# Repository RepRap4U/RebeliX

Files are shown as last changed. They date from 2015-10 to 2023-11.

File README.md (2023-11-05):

RebeliX X2
=======
RebeliX X2 – nová verze 3D tiskárny RebeliX. Tiskárna je šířena pod licencí GPLv3. 3D model, návod a seznam materiálu na stavbu naleznete ve složce "Manuals". Tiskárna je původně inspirovaná konstrukcemi Rebel II a Průša i3.

RebeliX X2 3D model tiskarny

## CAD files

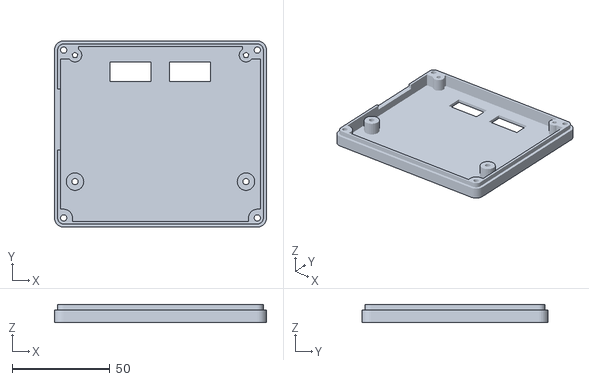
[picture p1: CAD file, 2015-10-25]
src/Doplnky/LCD/Case_for_the_Full_Graphic_Smart_LCD_Controller/Case_for_the_Full_Graphic_Smart_LCD_Controller-Bottom_Case_FGD.stl
108.6 x 95.4 x 9.30

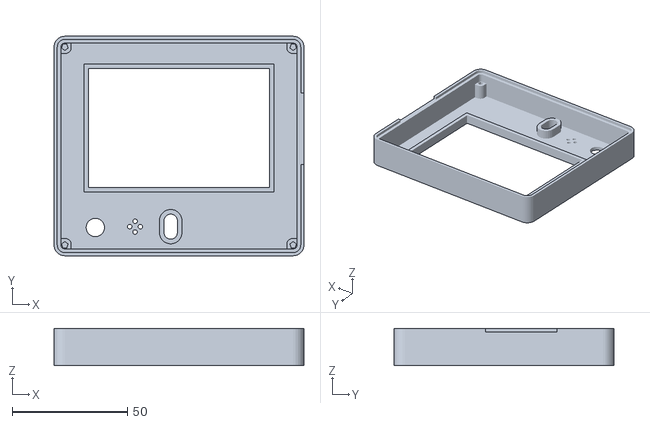
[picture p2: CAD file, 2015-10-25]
src/Doplnky/LCD/Case_for_the_Full_Graphic_Smart_LCD_Controller/Case_for_the_Full_Graphic_Smart_LCD-Top_Case_FGD.stl
108.6 x 95.4 x 16.1

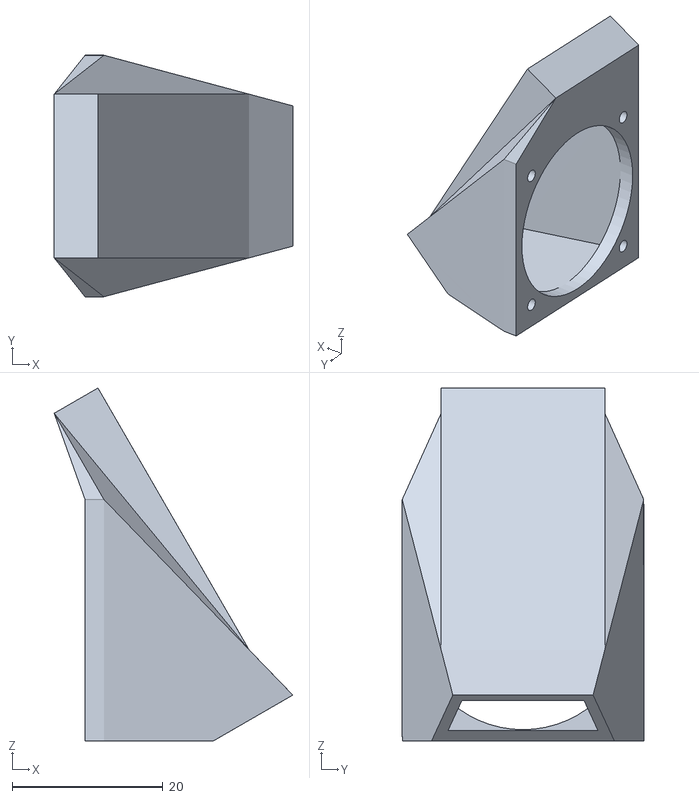
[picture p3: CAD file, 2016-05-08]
src/Extruder_filament_1.75mm/_Dual_experimental/inc/Fan_duct_30x30mm_base.stl
31.6 x 32.0 x 46.8

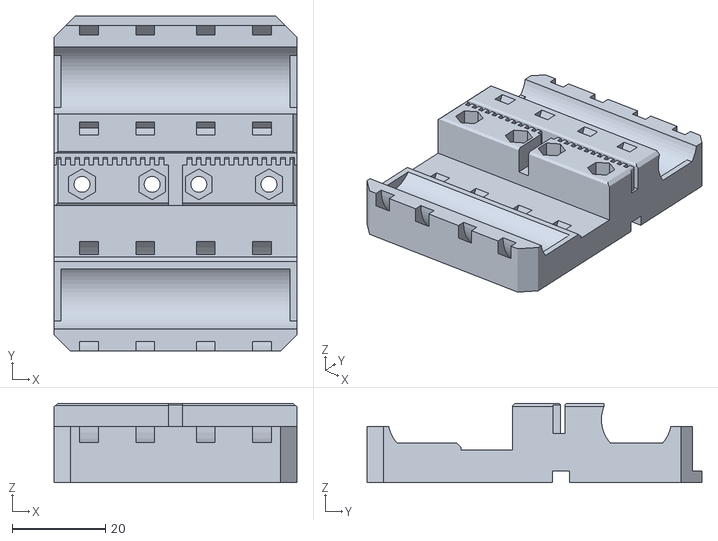
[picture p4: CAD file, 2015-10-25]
src/STLs/x-carriage-dual_GT2.stl
52.0 x 71.7 x 17.0

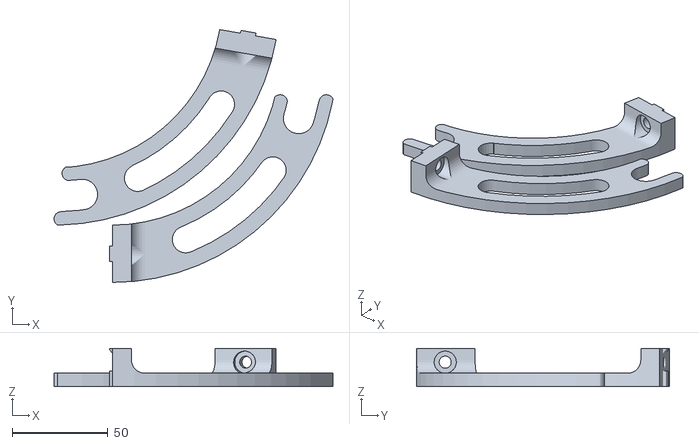
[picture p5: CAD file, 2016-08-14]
STL soubory/Doplnky/Drzak civky dual/spool-holder-dual.stl
146.0 x 132.3 x 20.0

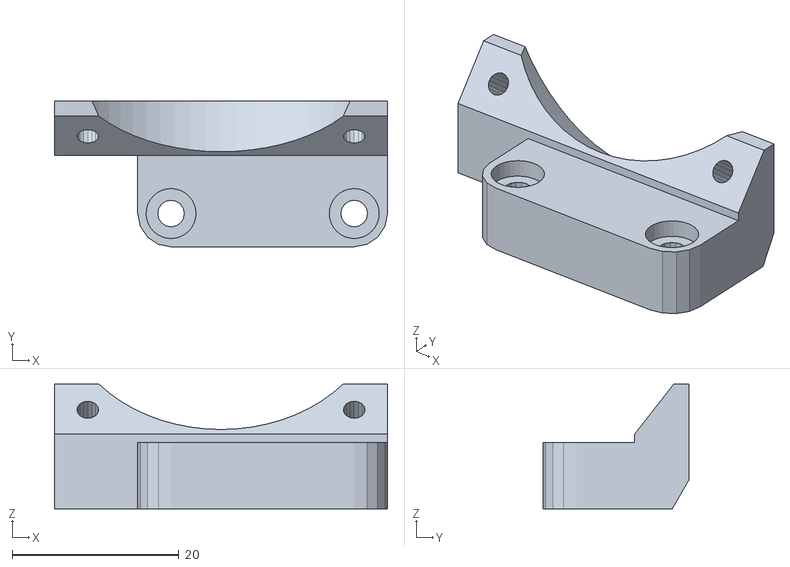
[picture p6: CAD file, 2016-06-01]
STL soubory/Doplnky/Fan drzak/40mm-fan-holder.stl
40.0 x 17.5 x 15.0

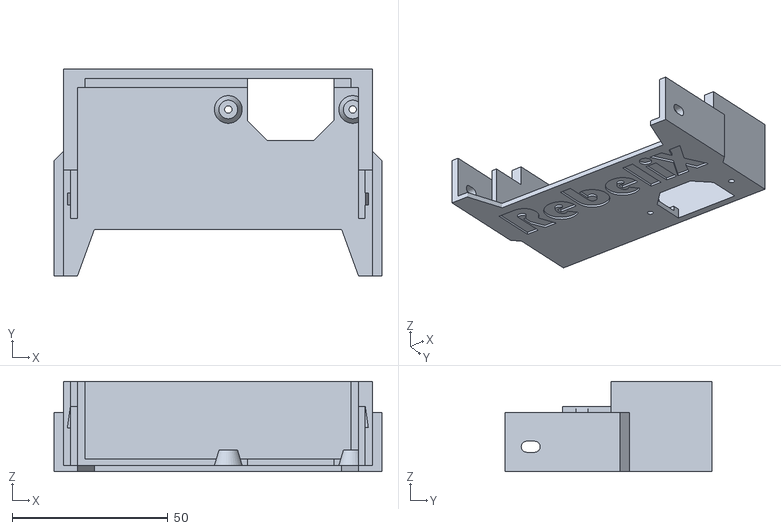
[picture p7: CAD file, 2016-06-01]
STL soubory/Doplnky/Kryt zdroje/Predni_kryt_EURO_12V_240W.stl
105.4 x 66.5 x 29.0

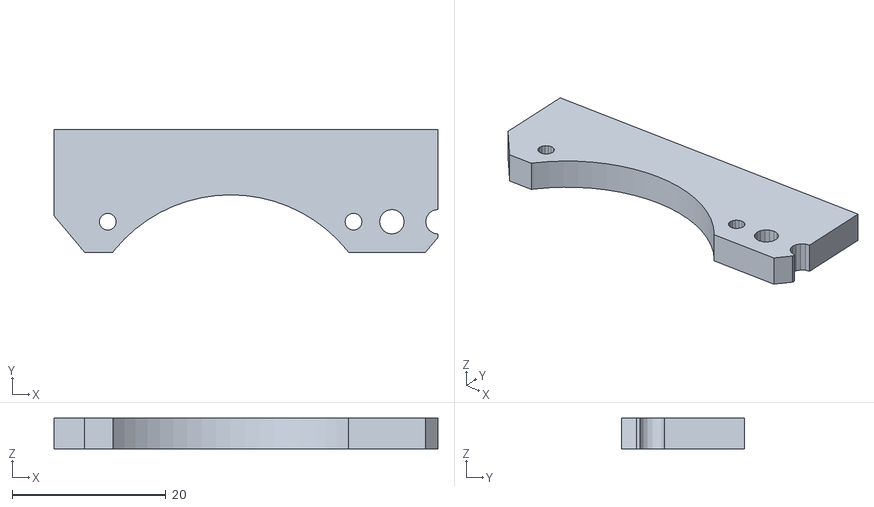
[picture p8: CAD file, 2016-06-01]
STL soubory/Doplnky/LED svetlo/50mm_LED_strip_holder.stl
50.0 x 16.0 x 4.00

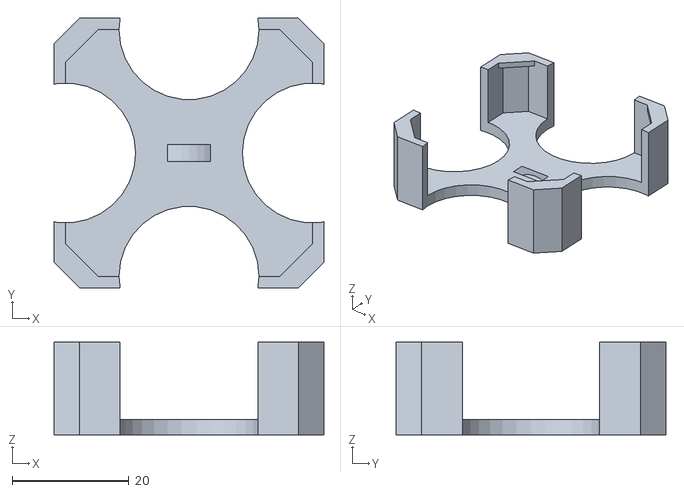
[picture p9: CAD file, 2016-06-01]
STL soubory/Doplnky/Nema 17 drzak kabelu/Nema17_cable_holder.stl
46.3 x 46.3 x 15.9

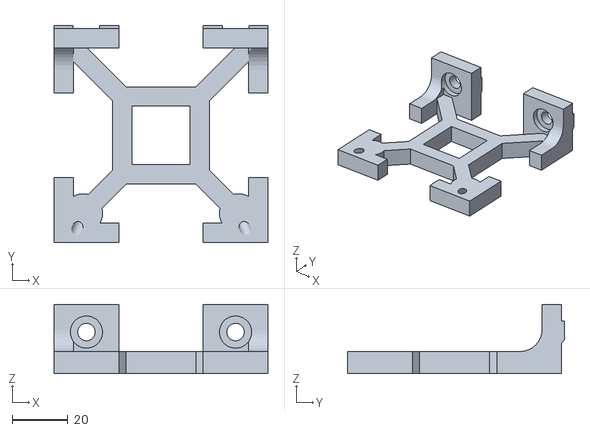
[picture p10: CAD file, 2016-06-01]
STL soubory/Doplnky/Vedeni filamentu dual/vedeni_filamentu_dual.stl
77.0 x 78.0 x 25.0

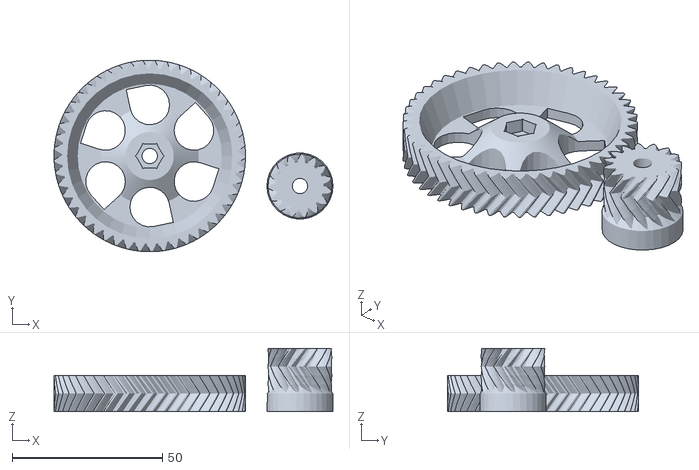
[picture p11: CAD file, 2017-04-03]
STL soubory/Extrudery/Classic_extruder_filament_1.75/wade-gears.stl
92.9 x 63.7 x 21.0

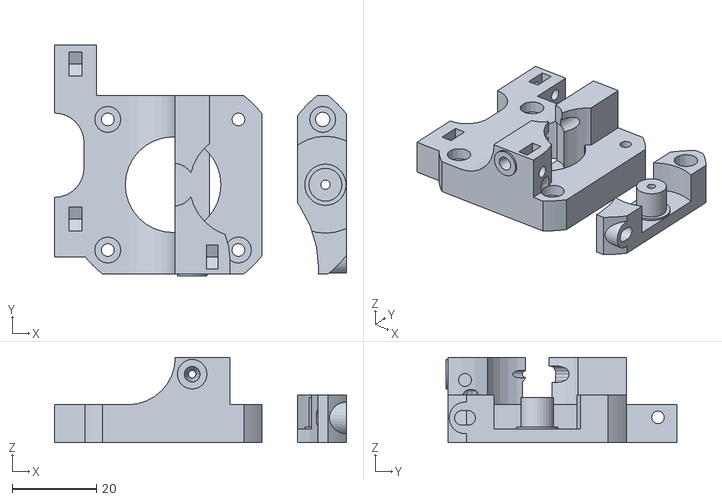
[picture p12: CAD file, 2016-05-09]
STL soubory/Extrudery/Dual_extruder_experimental_1.75/Dual_extruder_left.stl
69.3 x 54.8 x 20.2

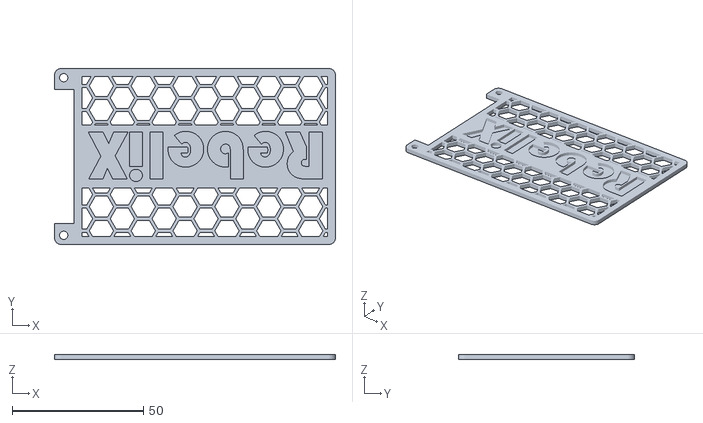
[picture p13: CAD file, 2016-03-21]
STL soubory/RAMPS_holder/RAMPS_cover.stl
107.0 x 67.0 x 2.00

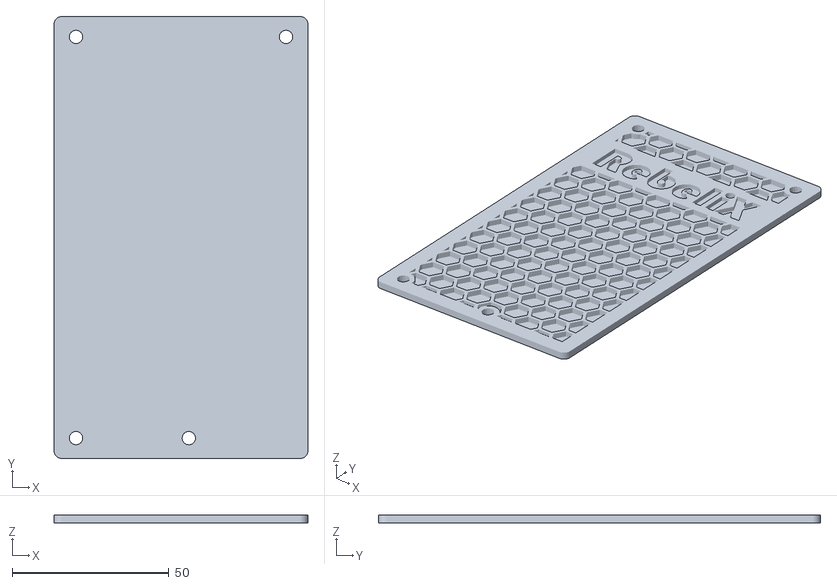
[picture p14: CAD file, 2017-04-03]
STL soubory/RUMBA_holder/RUMBA_cover.stl
81.0 x 141.0 x 2.50

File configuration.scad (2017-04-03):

/*
	Konfiguracni soubor 3D tiskarny RebeliX X2
	
	Sledujte nas na:		  
			www.RepRap4U.cz
			www.facebook.com/RebeliX.cz
			https://twitter.com/reprap4u
			https://plus.google.com/+Reprap4uCz-3Dtiskarna-RebeliX
*/

/*================ Slic3r nastaveni ==========================*/

// Vyska vrstvy pro tisknuti dilu [mm]
layer_height = 0.3;

// Sirka vytlacovaneho materialu [mm]
extrusion_width = 0.66; //Slic3r->Print Settings->Advanced->Default extrusion width

/*==================== M6 sroub ==============================*/

// Rezerva prumeru hlavy sroubu [mm]
space = 1;

// Prumer hlavy M6 sroubu (pricte se rezerva) [mm]
M6_head_diameter = 10.6+space;
//M6_head_diameter = 12+space;

// Prumer M6 sroubu
M6_dia = 6.3;

// Vyska hlavy M6 sroubu (dulezite pro zapusteni hlavy sroubu do plastu) [mm]
M6_head_height = 3.6;
//M6_head_height = 4.5;

// Delka sroubu M6 [mm]
// M6x12
M6_lenght = 12;

// Sirka matky do profilu (pokud neni pouzita, tak 0)
//profile_nut_width = 9.5;
profile_nut_width = 0;

/*=================== Nastaveni dilu =========================*/

// Posun Z zakladny
z_base_offset = 11;

// Posun Z motoru
z_motor_offset = 0;

// Tloustka rohovych spojek
// 5 mm => sroub M6x14 s podlozkou
// 3 mm => sroub M6x12 s podlozkou
coupler_thickness = 5;

// Prumer 8mm tyce
rod_8mm_d = 8.2;

// Posun drzacku mezi x-motor a x-end
x_holder_position = 6.5;

/*======================== Motory ============================*/

// Delka motoru (ovlivni dily a delky tyci pro osy Z a Y)
//SX17-1003LQFE (doporuceno hlavne na osu Z)
//motor_length = 29.5;
//SX17-1003 (doporuceno hlavne na osu Z), SX17-0503LQEF
motor_length = 34;
//SX17-1005
//motor_length = 40;
//SX17-0905 - zde je jiz problem s velkou vyskou motoru na ose Z - musi se upravit endstop-holder
//motor_length = 48;

/*================ Remeny a remenicky ========================*/

// GT2 
belt_tooth_distance = 2;
belt_tooth_ratio = 0.5;

// T2.5
//belt_tooth_distance = 2.5;
//belt_tooth_ratio = 0.68;

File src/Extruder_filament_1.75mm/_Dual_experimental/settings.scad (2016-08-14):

/*
	Konfiguracni soubor pro experimentalni dual extruder na RebeliX X2
	
	Sledujte nas na:		  
			www.RepRap4U.cz
			www.facebook.com/RebeliX.cz
			https://twitter.com/reprap4u
			https://plus.google.com/+Reprap4uCz-3Dtiskarna-RebeliX
*/

// Prumer chladice HE - urcuje minimalni vzdalenost trysek od sebe
HE_d = 19.5;

// Delka chladice
HE_l = 25;

// Pocet zeber chladice - mereno od spodni casti
// RebelMOD v3.0 - JRC (komplet)
pocet_zeber = 3;
//pocet_zeber = 5;

// Vzdalenost mezi tryskami
nozzle_distance = 19;

// Sirka extrudovane linky
extrusion_width = 0.6;

// Tloustka steny
width = 3*extrusion_width;

// Vyska vrstvy
layer_height = 0.3;

// Prumer teflonove trubicky (2 = bez teflonove trubicky)
//teflon_tube_diameter = 2;
teflon_tube_diameter = 4;

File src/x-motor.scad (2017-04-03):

// RebeliX
//
// x-motor
// GNU GPL v3
// Martin Neruda <neruda@reprap4u.cz>
// http://www.reprap4u.cz

include <../configuration.scad>

// Vertikalni korekce
v_corr = 0; //0.65;

x_rod_distance = 45 + v_corr;
motor_width = 42.3;
height = 13.5;
length = x_rod_distance+12;
pulley_diameter = 16;
// Tloustka endstopu (pro umisteni k motoru)
endstop_width = 6.5;

module x_motor_base(){
  cube([motor_width,length + 1,height],center=true);
  // Drzak Z endstopu
  translate([-motor_width/2,-length/2 -9,-height/2]) cube([25,10,5]);
  // Poutko na nacvaknuti k x-end  
  for(i = [4 : 4 : 8]){
	translate([-motor_width/2 - x_holder_position,-2,-height/2]){
		translate([0,-i,0]) cylinder(r=3,h=2-layer_height,$fn=32);
		translate([0,-i,0]) cylinder(r=2,h=5,$fn=32);
		translate([0,-3-i,0]) cube([5+x_holder_position,2*3,2-layer_height]);
		
		translate([-3,-8,0]) cube([5,2*2,2-layer_height]);
		translate([-2,-8,0]) cube([2*2,4,5]);
	}
  }
}

module x_motor_cuts(){
  translate([-motor_width/2+2,-length/2 + 6,height/2 - 1]) rod_cuts();
  translate([-motor_width/2+1,length/2 - 6,height/2 - 1]) rod_cuts();
  // Prisroubovani motoru
  translate([15.5,15.5,0])
  {
    translate([0,0,0]) cylinder(r=1.9,h=30,$fn=32,center=true);
	translate([2,0,0]) cylinder(r=1.9,h=30,$fn=32,center=true);
	translate([1,0,0]) cube([2,2*1.9,30],center=true);
	
	translate([-31,-31,0]) cylinder(r=1.9,h=30,$fn=32,center=true);
	translate([-29,-31,0]) cylinder(r=1.9,h=30,$fn=32,center=true);
	translate([-30,-31,0]) cube([2,2*1.9,30],center=true);
	
	translate([-31,0,0]) cylinder(r=1.9,h=30,$fn=32,center=true);
	translate([-29,0,0]) cylinder(r=1.9,h=30,$fn=32,center=true);
	translate([-30,0,0]) cube([2,2*1.9,30],center=true);
  }
  // Vyrez pro motor
  cylinder(r=11.5,h=30,$fn=64,center=true);
  // Vyrez pro remen
  translate([0,-11.5,-height/2 - 0.1]) cube([30,2*11.5,30]);
  
  // Vyrez pro endstop
  translate([0,-length/2 - 10,-height/2 - 1]) cube([30,30,20]);
  
  // Setreni plastem
  translate([-motor_width/2 - 0.1,-11.5,0]) cube([30,2*11.5,30]);
  // Serizle hrany
  translate([0,11.5,height/2+2.5]) rotate([45,0,0]) cube([motor_width + 1,5,5],center=true);
  translate([0,-11.5,height/2 + 2.5]) rotate([45,0,0]) cube([motor_width + 1,5,5],center=true);

  // Otvory pro pridelani ZIP pasky sroubky
  translate([-motor_width/2 + 5,-length/2 -2.5,0])
  cylinder(r=1.2,h=30,$fn=16,center=true);
  translate([-motor_width/2 + 15,-length/2 -2.5,0])
  cylinder(r=1.2,h=30,$fn=16,center=true);
  
  // Seriznuti drzaku na Z-endstop
  translate([-motor_width/2 -0.1,-length/2-9,-height/2 + 3.5]) rotate([45,0,0]) cube([25,10,5]); 
}

module rod_cuts(){
  // 8mm tyc
  translate([0,0,0]) rotate([0,90,0]) cylinder(r=4.1, h=100, $fn=32,center=true);
  // Vyrez pro ZIP pasky
  for( i = [12 : 18 : 36])
  {
    translate([i,0,0]) rotate([0,90,0]) difference()
	{
       cylinder(r=6.6, h=3.5, $fn=32, center=true);
	   cylinder(r=5, h=4, $fn=32, center=true);
    }
  }	
}

module endstop() {
  difference(){
    union(){
      // Telo endstopu
      translate([0,0,0]) color("blue") cube([10,20,endstop_width], center=true);
      // Vyvody
	  translate([-9,7,0]) cube([8,3,4],center=true);
      translate([-9,-7,0]) cube([8,3,4],center=true);
      // Spinac
      translate([5,7,0]) cube([3,3,4],center=true);
    }
  // Otvory pro zip pasku
  translate([-2,5,0]) cylinder(r=1.5,h=10,$fn=16,center=true);
  translate([-2,-5,0]) cylinder(r=1.5,h=10,$fn=16,center=true);
  }
  
}

module x_motor(){
  difference() {
    x_motor_base();
    x_motor_cuts();
  }
}  

x_motor();

// X-endstop
%translate([15,-length/2 + 6,height/2 - 2*4.1]) endstop();
// Z-endstop
%translate([-(motor_width - 2)/2 + 9,-length/2 -4.5,-height/2 -endstop_width/2]) mirror([1,0,0]) rotate([0,0,-90]) endstop();

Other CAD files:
STL soubory/LCD_Full_Graphic/LCD_front.stl
STL soubory/z-top.stl
STL soubory/Doplnky/Kryt zdroje/Zadni_kryt_EURO_12V_240W.stl
src/Extruder_filament_1.75mm/inc/parametric_involute_gear_v5.0.scad
STL soubory/Extrudery/Classic_extruder_filament_1.75/gregs-wade-filament-175.stl
STL soubory/Extrudery/Classic_extruder_filament_1.75/nozzle_mount.stl
STL soubory/Extrudery/Dual_extruder_experimental_1.75/Dual_extruder_right.stl
STL soubory/Extrudery/Dual_extruder_experimental_1.75/Dual_nozzles_holder.stl
STL soubory/Extrudery/Dual_extruder_experimental_1.75/Fan_duct_30x30mm.stl
STL soubory/Extrudery/Dual_extruder_experimental_1.75/Nozzles_30mm_fan_holder.stl
STL soubory/Extrudery/Flexible_extruder_filament_1.75/gregs-wade-filament-175_Flexible.stl
STL soubory/Extrudery/Flexible_extruder_filament_1.75/nozzle_mount.stl
STL soubory/LCD_Full_Graphic/LCD_back.stl
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

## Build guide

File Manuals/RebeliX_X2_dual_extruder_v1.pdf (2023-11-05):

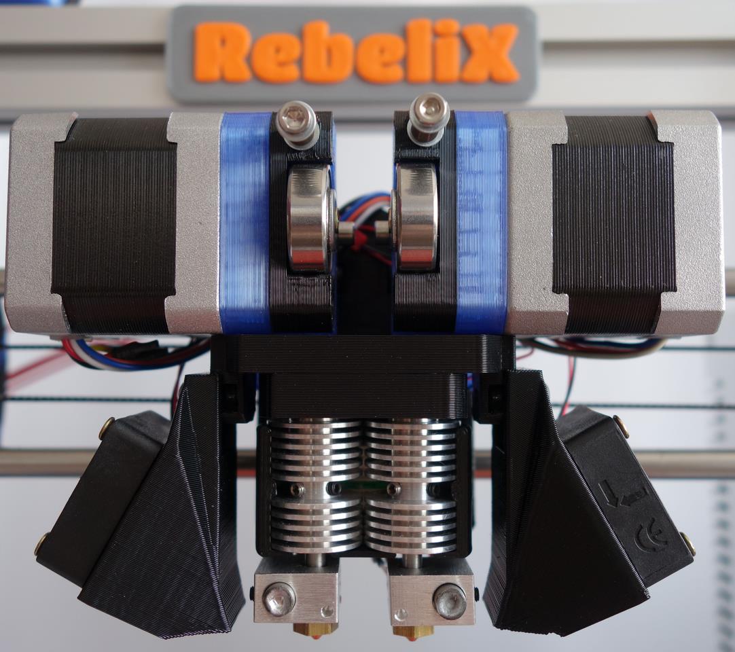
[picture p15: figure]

©2016 Martin Neruda | www.RebeliX.cz

# RebeliX X2

# www.RebeliX.cz

# Návod na dual extruder (hardware)

### Úvod

Autor dokumentu: | Vizitka:

### Martin Neruda (neruda@rebelix.cz)

### Stránky projektu: www.RebeliX.cz www.RepRap4U.cz

Pokud nechcete přijít o žádné novinky, přidejte si 3D tiskárnu RebeliX do oblíbených na Facebooku.

### www.facebook.com/rebelix.cz

### Změny

v1 (7. 5. 2016) – Počáteční verze

### Obsah

### Seznam netisknutého materiálu

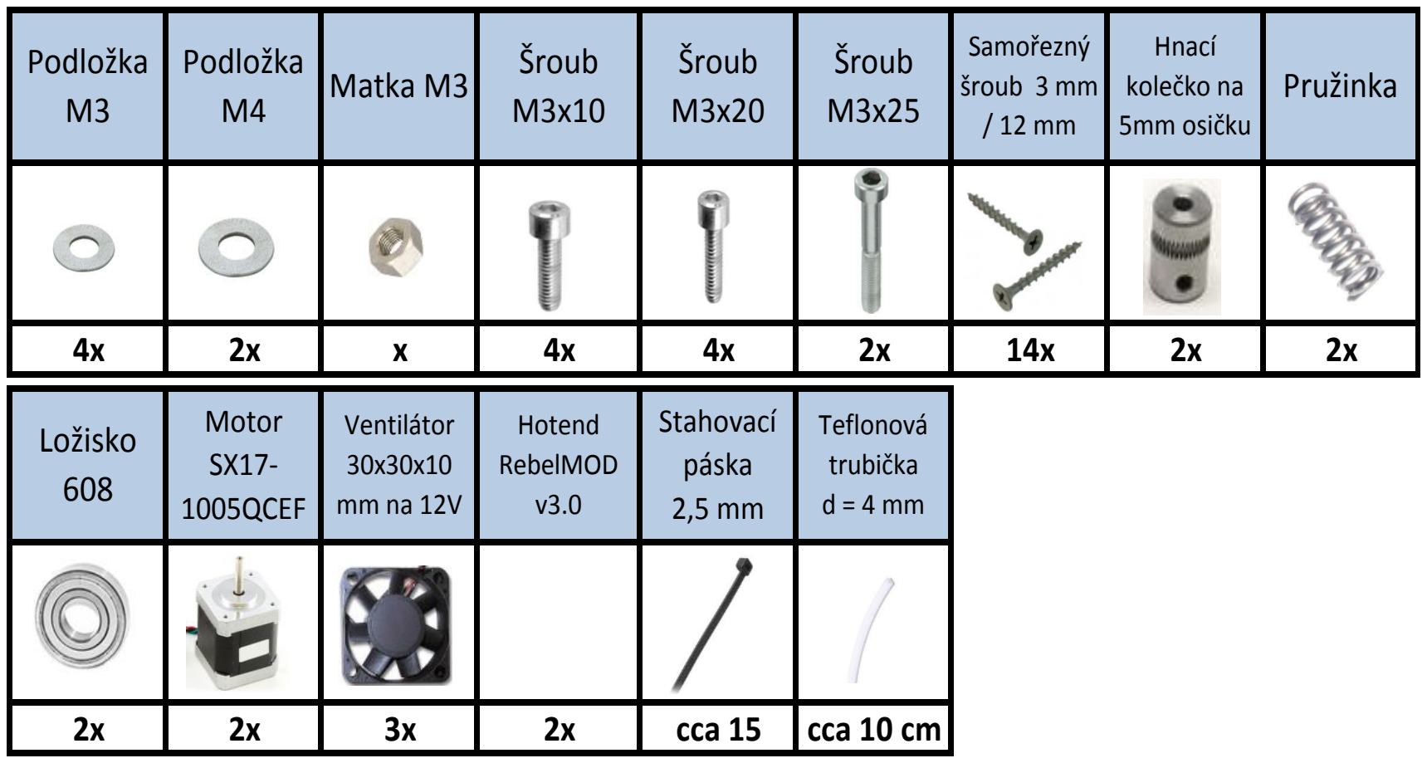
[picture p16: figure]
cca 15; cca 10 cm; Hnací kolečko na 5mm osičku; Pružinka; Ložisko 608; Motor SX17- 1005QCEF; Ventilátor 30x30x10 mm na 12V; Hotend RebelMOD v3.0; Stahovací páska 2,5 mm; Teflonová trubička d = 4 mm; Šroub M3x25; Samořezný šroub 3 mm / 12 mm; Podložka M3; Podložka M4; Matka M3; Šroub; Šroub M3x20

### Seznam tištěných dílů

Dual nozzles holder

Fan duct 30 x 30 mm

1x

Dual extruder right

1x | 1x Nozzles 30mm fan holder

1x

Dual extruder left

1x

x-carriage

1x

### Držák hotendů

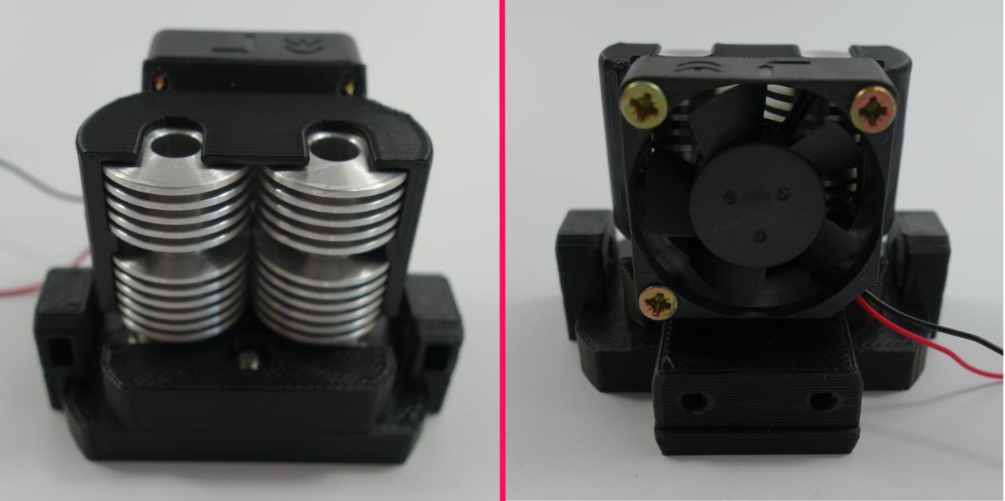
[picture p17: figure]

Netisknutý materiál:

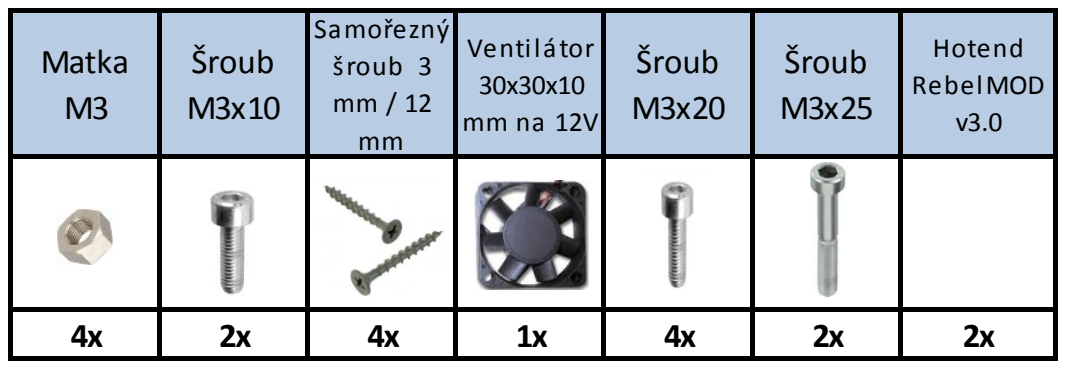
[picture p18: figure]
Ventilátor 30x30x10 mm na 12V; Šroub M3x25; Samořezný šroub 3 mm / 12 mm; Matka M3; Šroub M3x10; Šroub M3x20; Hotend RebelMOD v3.0

Tištěné díly:

Dual nozzles holder

1x | 1x Nozzles 30mm fan holder

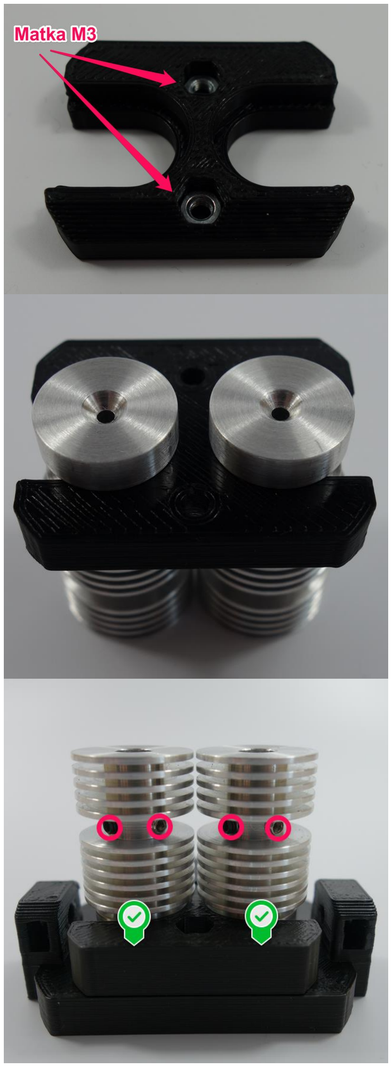
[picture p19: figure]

- Do plastového dílu „Dual nozzles holder“ zamáčkneme matky.
- Nasuneme oba chladiče.
- Chladiče natočíme tak, aby šroubky (červíci) směřovaly směrem, který je na obrázku (kvůli přístupu k šroubkům po sestavení extruderu).

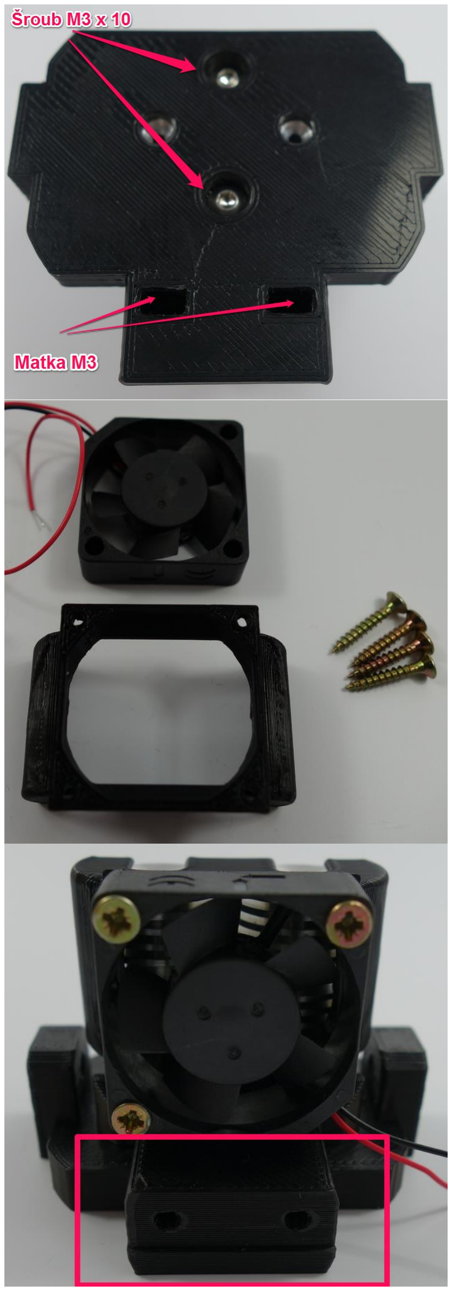
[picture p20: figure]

- Celek s chladiči sešroubujeme se základnou.
- Do otvorů vložíme matky.
- Přišroubujeme 30 mm ventilátor na plastový díl „Nozzles 30mm fan holder“.
- Držák ventilátoru nacvakneme na chladiče.

### Direct extruder (levý a pravý)

Netisknutý materiál:

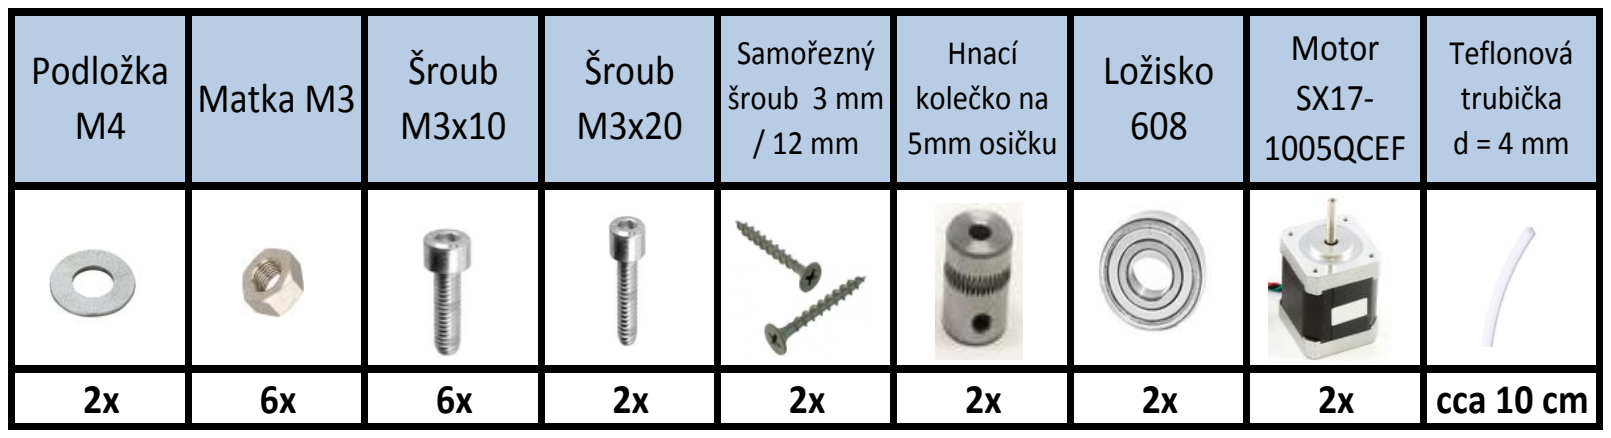
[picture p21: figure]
cca 10 cm; Podložka M4; Matka M3; Šroub; Šroub M3x10; Hnací kolečko na 5mm osičku; Teflonová trubička d = 4 mm; Ložisko 608; Motor SX17- 1005QCEF; Samořezný šroub 3 mm / 12 mm

Tištěné díly:

Dual extruder left

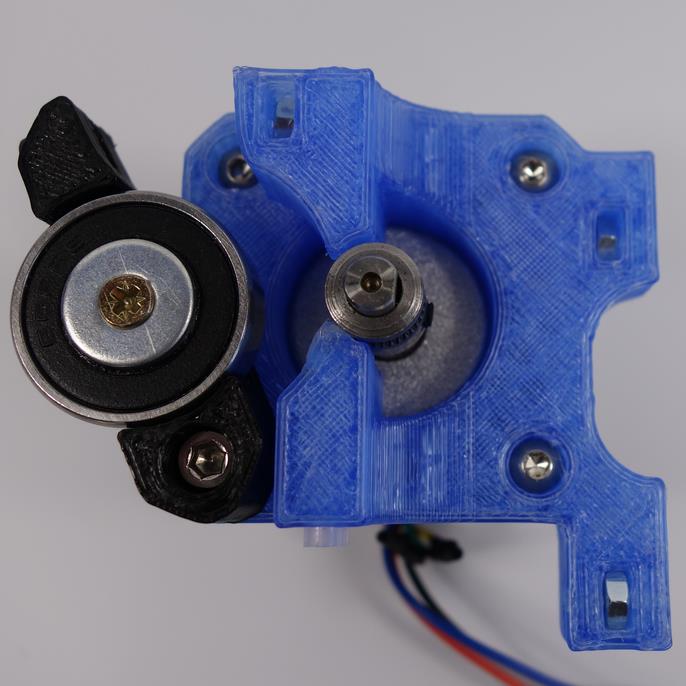
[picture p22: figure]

1x | 1x Dual extruder right

Stejný postup sestavení platí pro levý i pravý extruder.

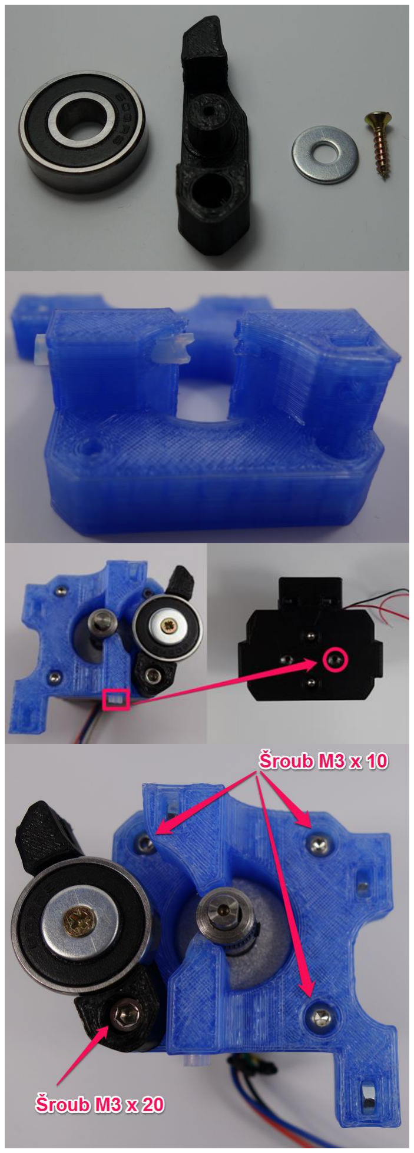
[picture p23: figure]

- Na plastový díl nasadíme ložisko a zajistíme samořezným šroubkem s podložkou.
- Do plastového dílu extruderu zatlačíme teflonovou trubičku a necháme ji kousek přečnívat za tělo extruderu.
- Přečnívající teflonová trubička nám později zajistí, že po sesazení extruderu a základny bude extruder a základna s hotendy (otvory pro filament) v jedné ose.
- Plastový díl extruderu nasadíme na motor a přišroubujeme.
- Přišroubujeme i díl s přítlačným ložiskem.
- Na osičku motoru nasadíme hnací kolečko a dle potřeby seřízneme teflonovou trubičku tak, aby nedřela o hnací holečko.

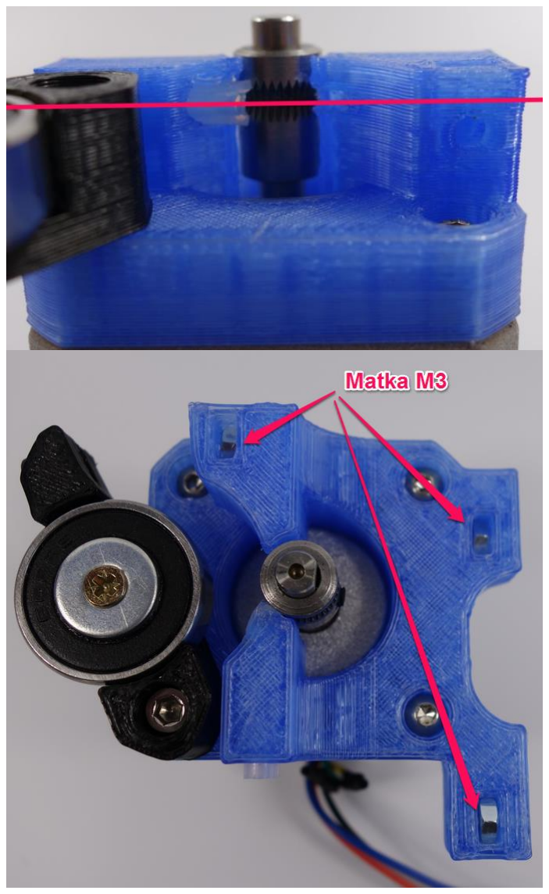
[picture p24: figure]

- Drážku v hnacím kolečku dáme do roviny s otvorem pro filament a řádně dotáhneme červíka na hnacím kolečku.
- Do otvoru držáku přítlaku a držáku extruderu zatlačíme matky.

### Kompletace dual extruderu

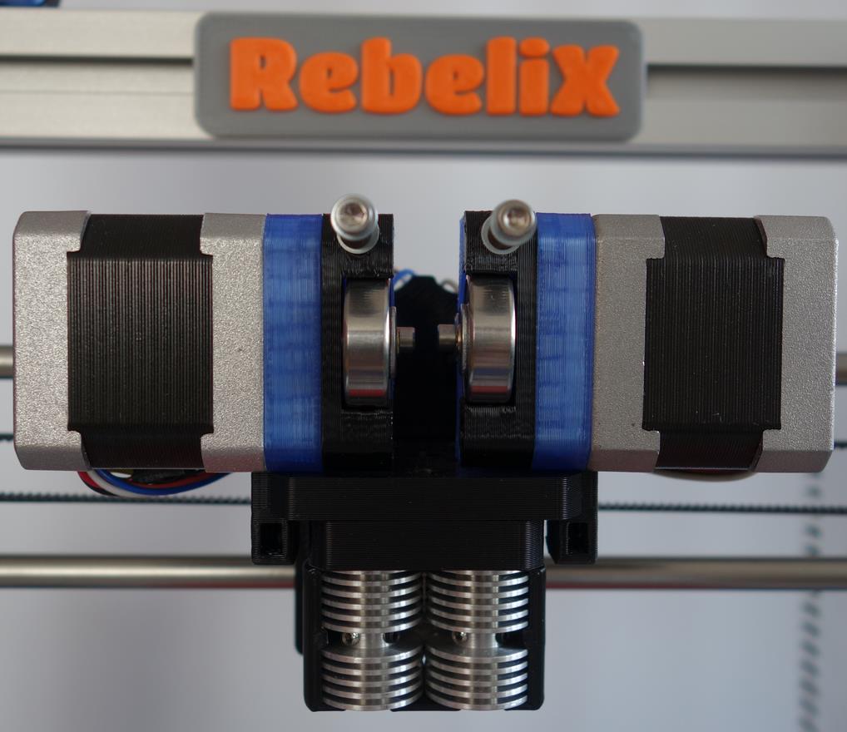
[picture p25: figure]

Netisknutý materiál:

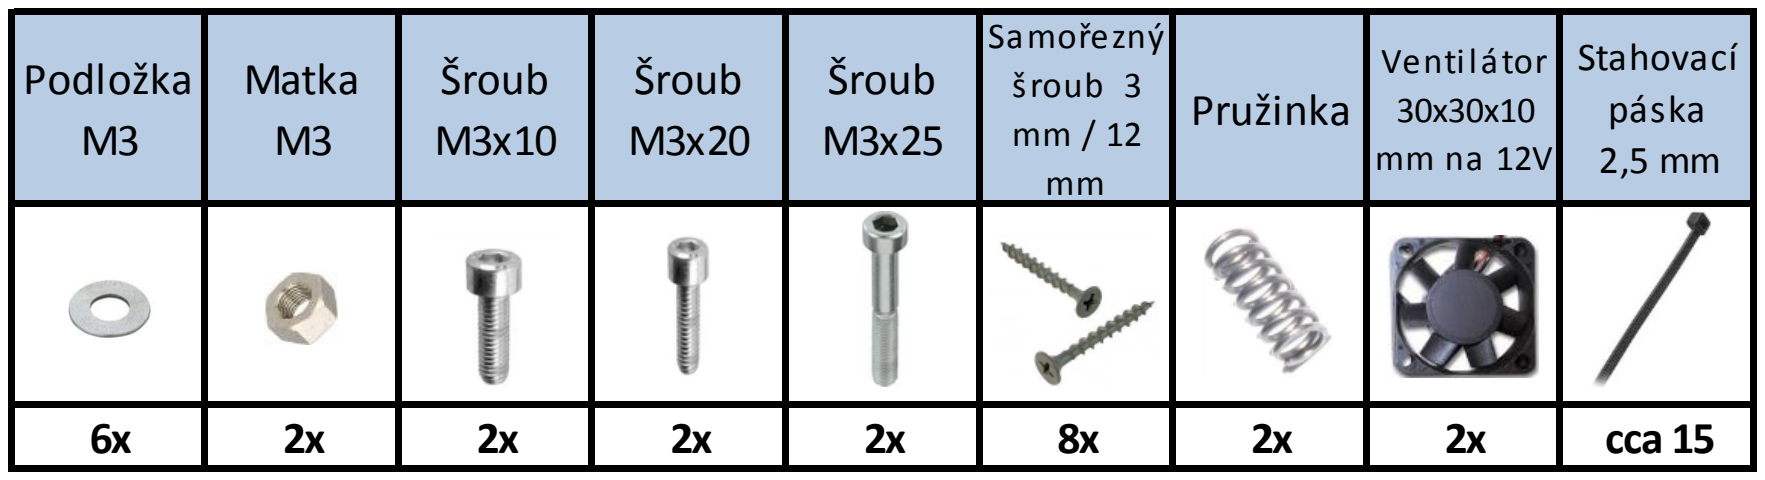
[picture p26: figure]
cca 15; Stahovací páska 2,5 mm; Šroub M3x25; Podložka M3; Matka M3; Šroub M3x10; Šroub M3x20; Samořezný šroub 3 mm / 12 mm; Pružinka; Ventilátor 30x30x10 mm na 12V

Tištěné díly:

Fan duct 30 x 30 mm

2x | 1x x-carriage

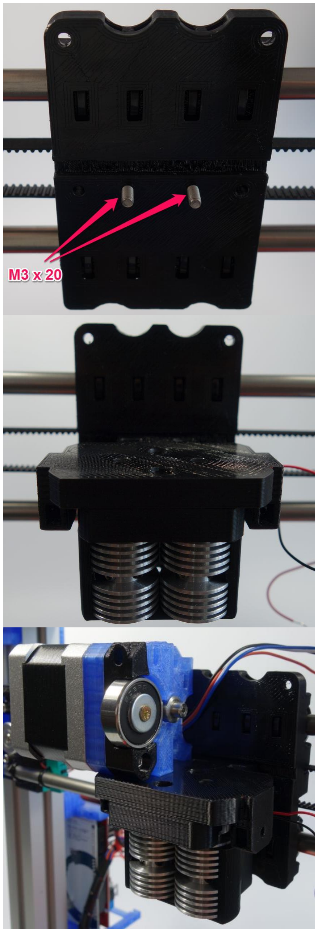
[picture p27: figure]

- Vyměníme vozík (x-carriage).
- Ze zadní strany vozíku zasuneme dva šrouby.
- Držák s chladiči hotendů přišroubujeme na vozík.
- Nasadíme levý a pravý extruder a přišroubujeme k vozíku.

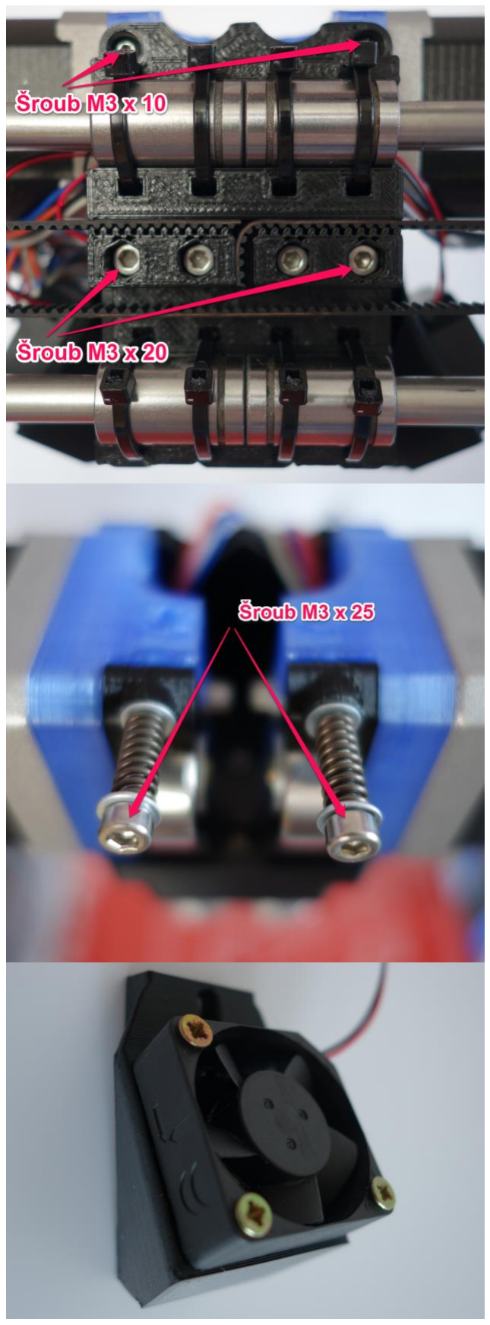
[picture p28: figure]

- Na přítlačná ložiska nasadíme šroubky s pružinkami a jednou podložkou na každé straně.
- Na plastový díl „Fan duct 30x30 mm“ (ventilátor na chlazení objektu) přišroubujeme 30 mm ventilátor.

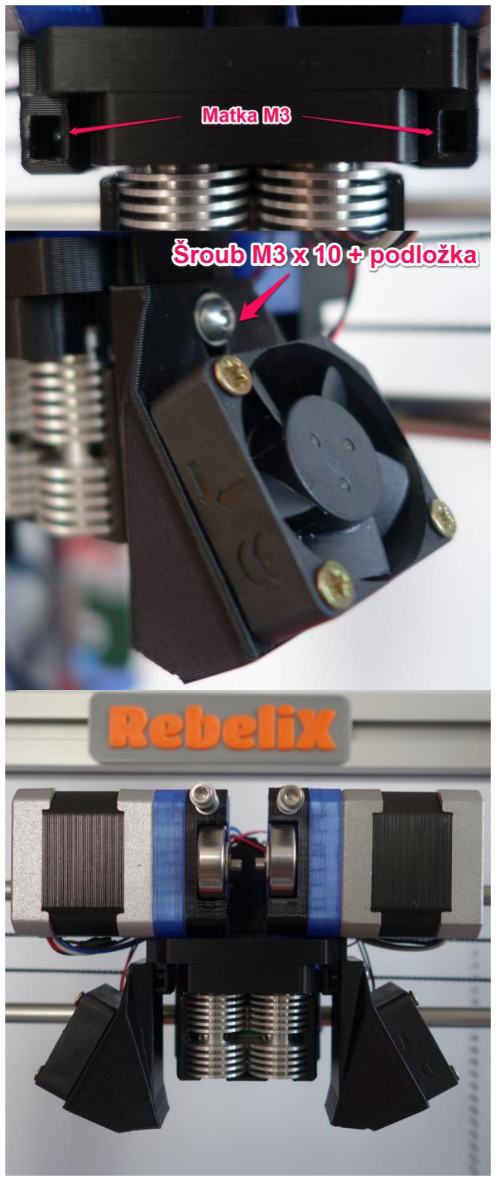
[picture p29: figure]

- Do otvorů na držáku zasuneme matky.
- Přiděláme držáky ventilátorů.
- Po mechanické stránce máme dual extruder hotový

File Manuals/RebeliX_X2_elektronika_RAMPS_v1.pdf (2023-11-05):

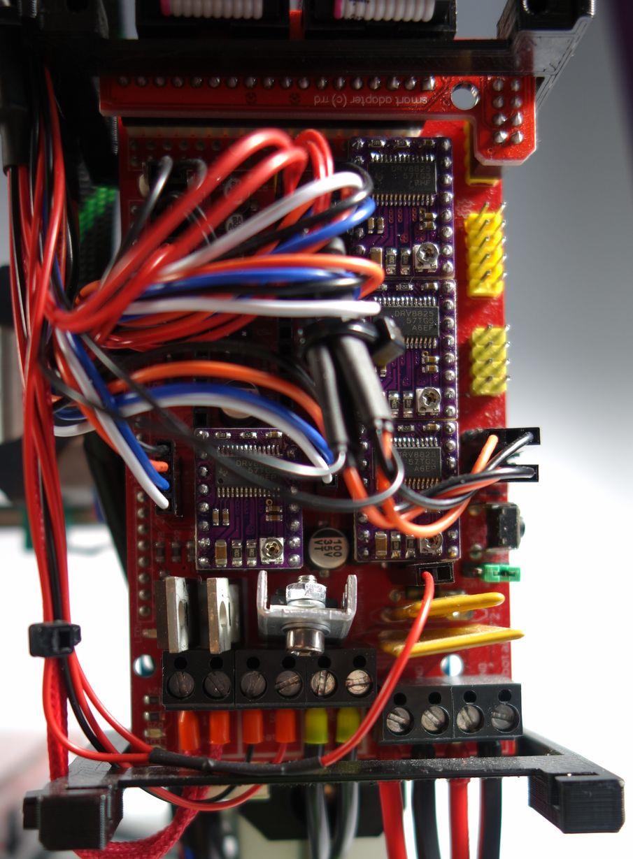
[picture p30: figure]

©2016 Martin Neruda | www.RebeliX.cz

# RebeliX X2

# www.RebeliX.cz

# Zapojení elektroniky

# (RAMPS 1.4)

Úvod

Autor dokumentu: | Vizitka:
Martin Neruda (neruda@rebelix.cz)

Stránky projektu:
www.RebeliX.cz
www.RepRap4U.cz

Pokud nechcete přijít o žádné novinky, přidejte si 3D tiskárnu RebeliX do oblíbených na Facebooku.
www.facebook.com/rebelix.cz

Změny

v1 (23. 5. 2016) – Počáteční verze

Obsah

Bezpečnostní pokyny
- Zařízení pracuje na síťovém napětí 230V, které je při doteku životu nebezpečné. Je nutno dbát zvýšené opatrnosti a nesahat na přívodní kontakty, když je zařízení pod napětím! Manipulovat se zapojením přívodu síťového napětí 230V smí pouze osoba s příslušnou kvalifikací dle vyhlášky 50/1978 Sb. Jinak konáte na vlastní riziko!
- Nikdy nenechávejte zapnuté zařízení bez dozoru.
- Nikdy nenechávejte děti používat zařízení bez dohledu.
- Nepoužívejte toto zařízení s poškozeným přívodním kabelem, nebo zástrčkou, nebo pokud má zařízení poruchu či bylo nějakým způsobem poškozeno.
- Zařízení vždy vypněte ze zásuvky, když je bez dozoru nebo manipulujete s elektronikou.
- Autor materiálu nenese žádnou zodpovědnost za případné újmy na zdraví či majetku. Vše děláte na vlastní nebezpečí.

Elektronika RAMPS 1.4

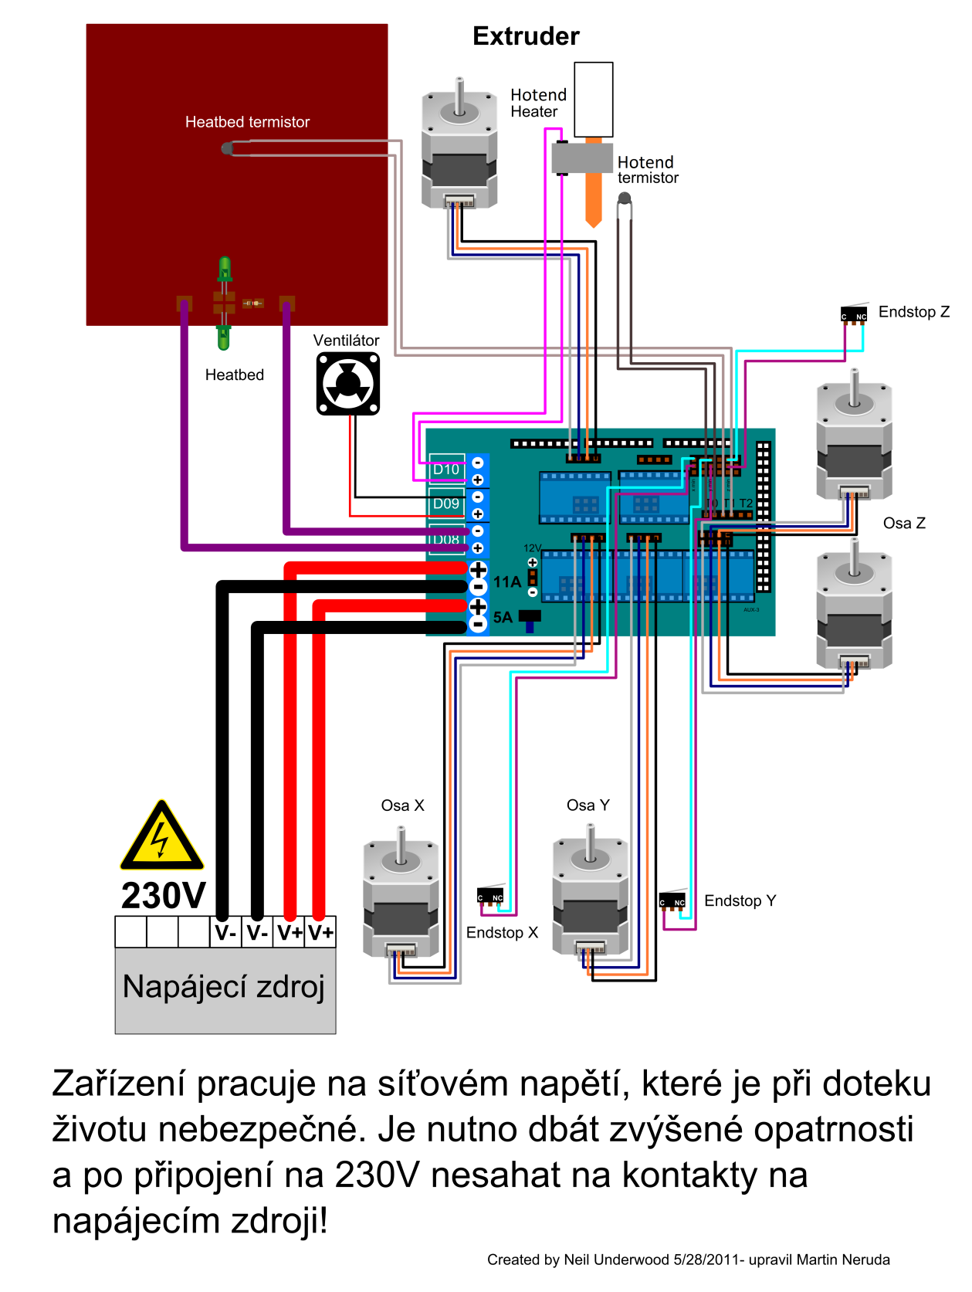
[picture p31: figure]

Připojení napájecího zdroje

Na kabely nasuneme plastovou průchodku a opatrně (aby nedošlo k poškození izolace vodičů) je protáhneme hliníkovým profilem.

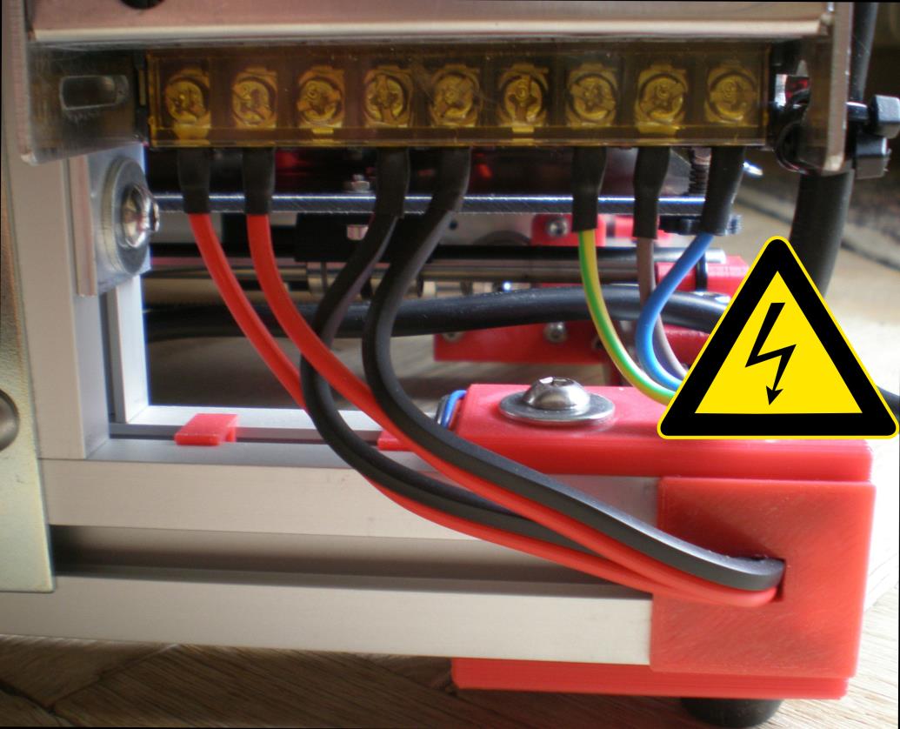
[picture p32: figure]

! Varování !
Zařízení pracuje na síťovém napětí 230V, které je při doteku životu nebezpečné. Je nutno dbát zvýšené opatrnosti a nesahat na přívodní kontakty, když je zařízení pod napětím! Manipulovat se zapojením přívodu síťového napětí 230V smí pouze osoba s příslušnou kvalifikací dle vyhlášky 50/1978 Sb. Jinak konáte na vlastní riziko!

Na druhé straně kabely opět protáhneme plastovou průchodkou.

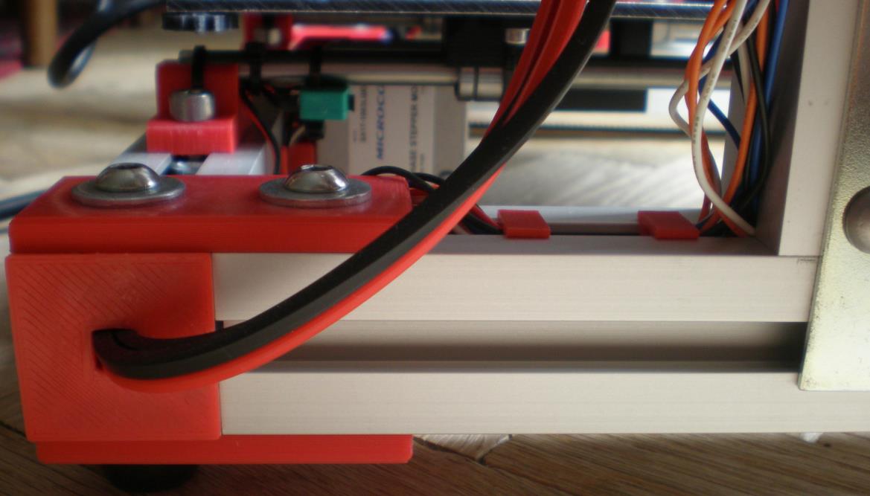
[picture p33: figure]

Dejte velký pozor na správnou polaritu připojovaných vodičů od napájecího zdroje, aby nedošlo k poškození elektroniky! Vodiče ve svorkovnici pečlivě dotáhneme, aby nevznikl přechodový odpor (svorkovnice by se průchodem proudu zahřívala a mohlo by dojít k jejímu poškození / případně požáru).

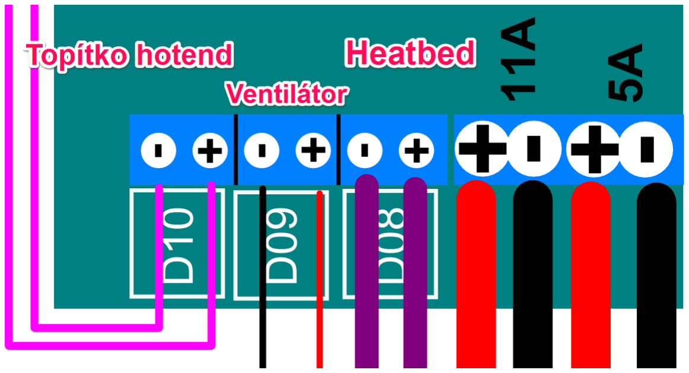
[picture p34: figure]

Připojení heatbed, topítka hotendu a ventilátoru

U topítka hotendu a heatbed není nutné dbát na polaritu (topné těleso je rezistor) – znovu je nutné pečlivě dotáhnout vodiče ve svorkovnici (D10, D8). Ventilátor (Fan) připojíme dle předešlého schématu.

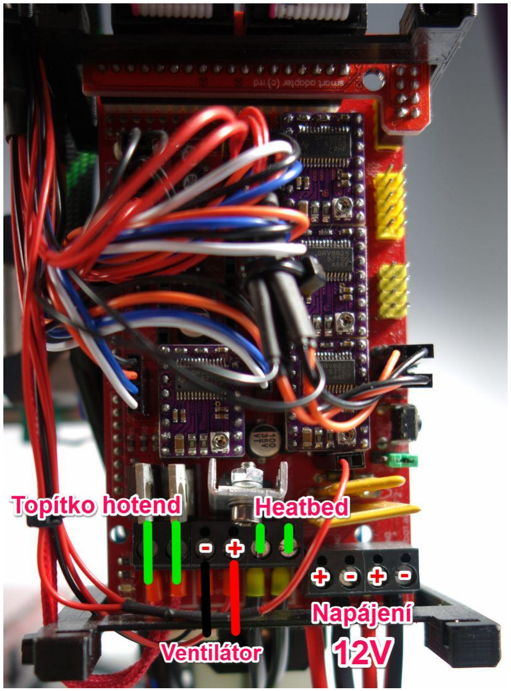
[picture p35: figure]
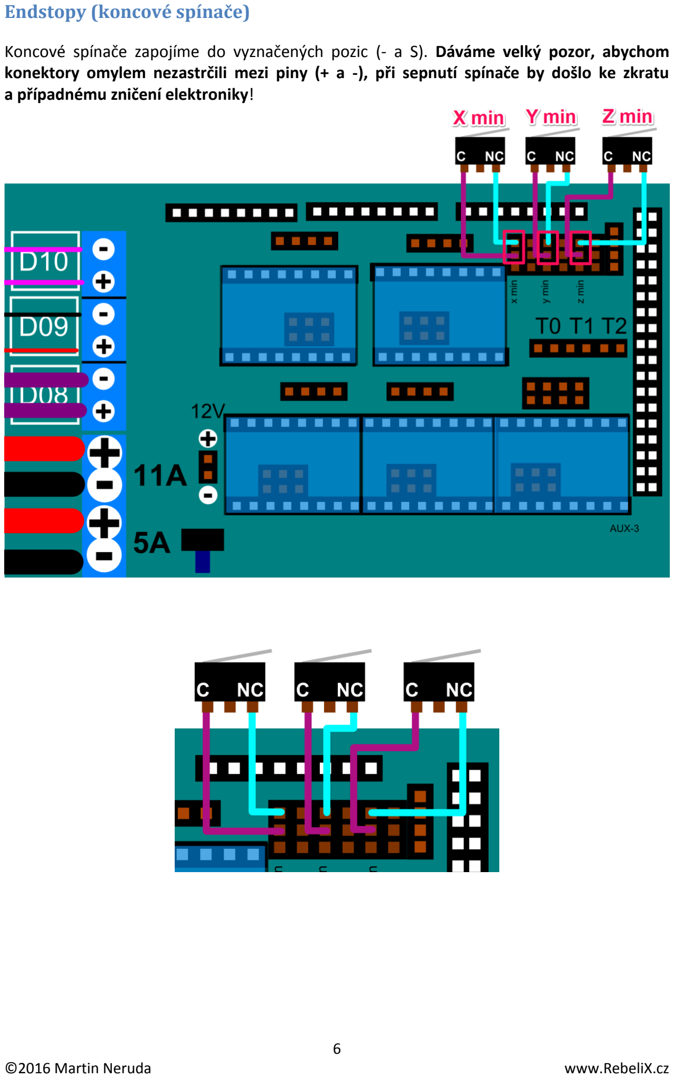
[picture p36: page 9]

Endstopy (koncové spínače)

Koncové spínače zapojíme do vyznačených pozic (- a S). Dáváme velký pozor, abychom konektory omylem nezastrčili mezi piny (+ a -), při sepnutí spínače by došlo ke zkratu a případnému zničení elektroniky!

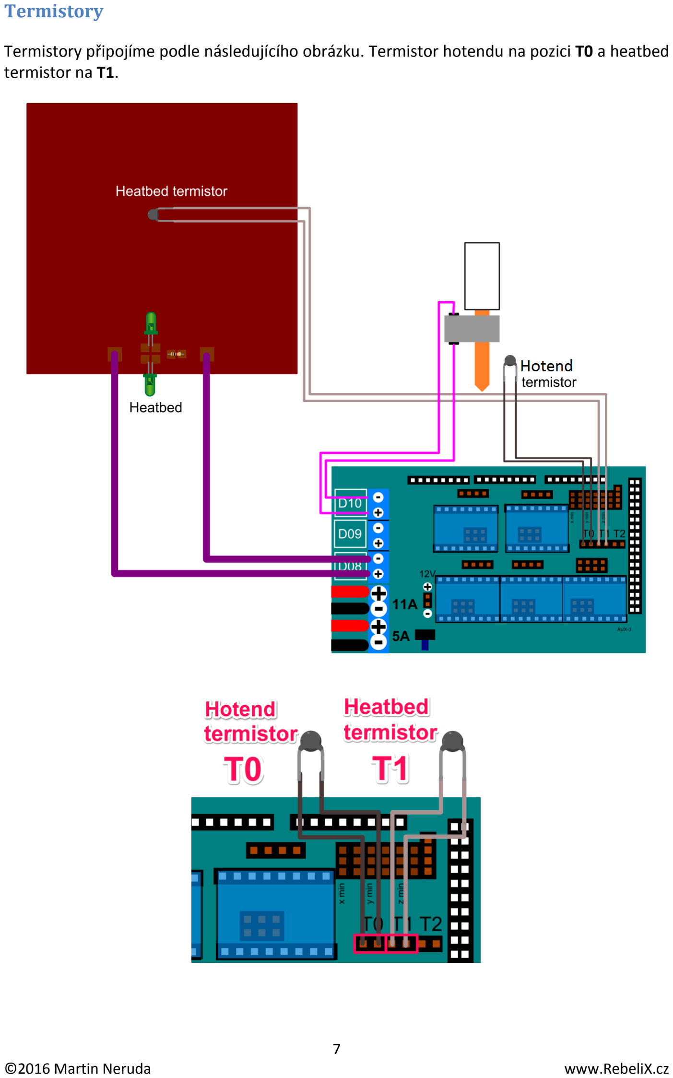
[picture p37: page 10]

Termistory

Termistory připojíme podle následujícího obrázku. Termistor hotendu na pozici T0 a heatbed termistor na T1.

Motory

Motory mají čtyři vodiče (sériové zapojení). Zapojení v konektoru je v následujícím pořadí (černý, oranžový, modrý, bílý).

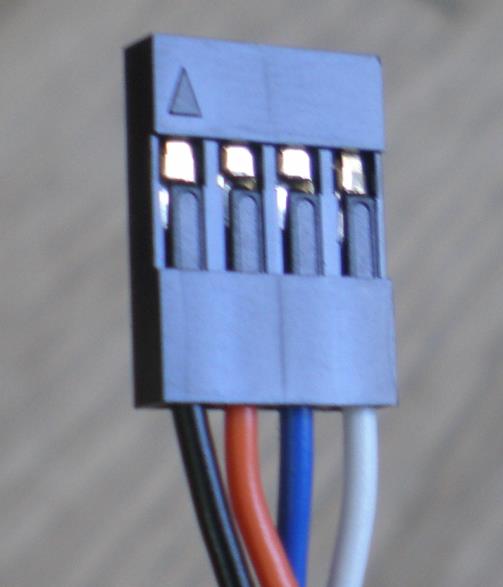
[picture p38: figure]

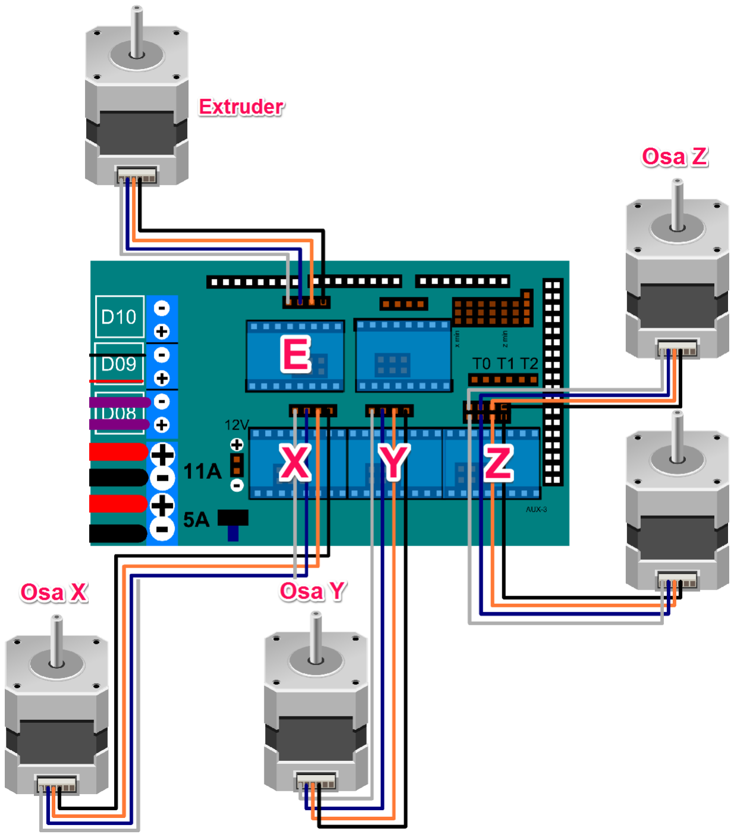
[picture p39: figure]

Driver krokových motorů

Drivery krokových motorů vždy připojujeme / odpojujeme při odpojeném napájecím napětí, aby nedošlo k jejich poškození. Na destičce driveru většinou bývá označení jednotlivých vývodů (musí korespondovat s označením na RAMPS desce, aby nedošlo k otočení nebo nesprávnému nasunutí driveru). Pozor na to, že drivery DRV8825 a A4988 mají obráceně trimry.

Zapojení driverů DRV8825:

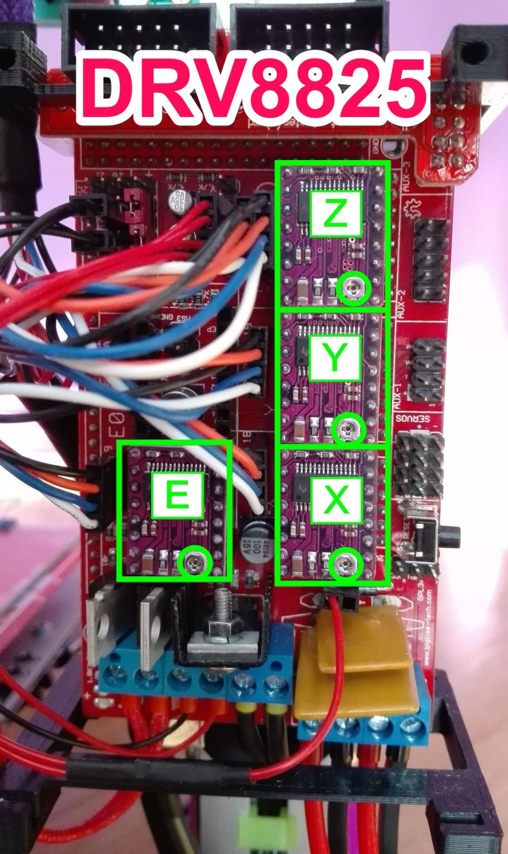
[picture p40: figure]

Zapojení driverů A4988:

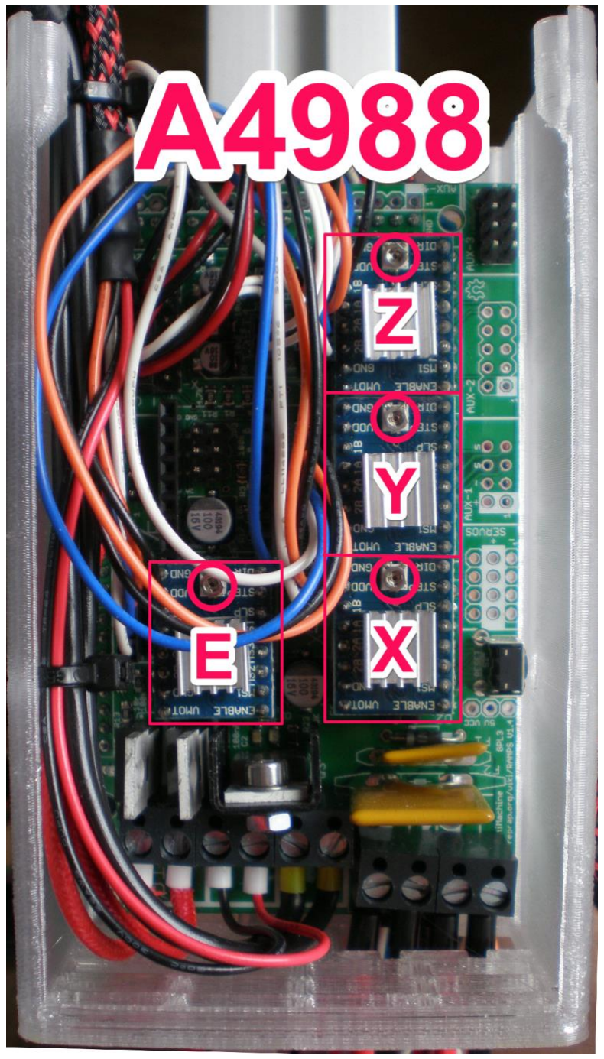
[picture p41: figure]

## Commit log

2014-04-09 Zmena nazvu corner-clutch.scad na corner-coupler.scad
    [corner-coupler.scad]
2014-04-10 Opraveny include na configuration.scad
    [gregs-wade-v3.scad]
2014-05-29 Hlubsi zapusteni M6 sroubu u z-bottom
    [z-bottom.scad]
2014-08-08 Uprava drzaku na pridelani spinace ZIP paskou
    [z-endstop-holder.scad]
2014-08-08 Presun do nove slozky Extruder_filament_3mm
    [bearing-guide.scad, conf_bushing.scad, extruder-idler.scad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]
2014-08-08 Mini drzak RAMPS elektroniky
    [RAMPS_mini.scad]
2014-08-08 Upravene otvory pro ZIP pasky
    [SlidingBoxV13.scad]
2014-08-08 Stred pro prumery dvou civek
    [spool-center.scad]
2014-08-08 Upraveny drzak civky pro pouziti spool_bearing
    [spool-holder.scad]
2014-08-08 Trubicka proti zarezavani zavitove tyce do spool-holder
    [spool_bearing.scad]
2014-08-08 Pridana moznost napinani remenu motorem
    [x-end-motor.scad]
2014-08-08 Zvetsena mezera mezi tyci a plastem
    [y-rod-holder.scad]
2014-08-08 Drzak 40mm ventilatoru pro tisk z PLA
    [j-head-mount.scad]
2014-10-26 Extruder pro filament 1.75 mm
    Upraveny extruder pro strunu 1.75 mm
    [bearing-guide.scad, conf_bushing.scad, extruder-idler.scad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]
2014-12-02 Krabicka na RAMBO elektroniku
    Zakrytovani RAMBO elektroniky
    [RAMBO_cover_back.stl, RAMBO_cover_front.stl, RAMBO_holder.stl]
2015-10-25 Upgrade na verzi RebeliX X2
    Mezi hlavni zmeny patri:
    - dily optimalizovane pro snadnejsi tisk a stavbu
    - mensi pocet ruzneho spojovaciho materialu
    - priprava osy X na dvoutryskovou verzi (4 loziska LM8UU pro vetsi
    stabilitu)
    - plastove domecky lozisek nahrazeny lozisky 624 (nehrozi rozpadnuti
    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
    [40mm-fan-holder.scad, 50mm_LED_strip_holder.scad, Case_for_the_Full_Graphic_Smart_LCD-Top_Case_FGD.stl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]
2015-11-03 Zmena uchyceni hot-endu v extruderu
    Zmena uchyceni HE ze "slot-in" za klasicky drzak - lepe se tiskne a pro
    vymenu HE neni nutne sundavat cely extruder. Pro uchyceni HE je potreba:
    1x M3x16
    1x M3x25
    2x matka M3 a 2x podlozka
    [gregs-wade-filament-175.scad, gregs-wade-filament-175.stl, nozzle_mount.scad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]
2015-11-04 Prejmenovani a drobna kosmeticka uprava
    x-carriage pro single extruder
    [x-carriage.scad, x-carriage_GT2.stl]
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2015-11-12 STL uprava sloupku pro prisroubovani LCD
    [mods_for_display_case_front.stl]
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2016-01-13 Kryt zdroje s textem
    Kryt na prumyslovy zdroj 12V / 240W nebo 350W
    [Predni_kryt_EURO_12V_240W.scad, RebeliX.stl, Zadni_kryt_EURO_12V_240W.scad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]
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2016-03-06 Uprava drzaku pro 40 mm fan na extruderu
    [40mm-fan-holder.scad]
2016-03-06 Upraveny extruder pro tisk flexibilnich materialu
    Experimentalni extruder pro tisk flexibilnich materialu s moznosti
    vyndani hnaciho kolecka. Nastaveni v
    gregs-wade-filament-175_Flexible.scad:
    teflon_tube = 1 -> teflonova trubicka s prumerem 4mm v tele extruderu
    teflon_tube = 0 -> bez teflonove trubicky
    [gregs-wade-filament-175_Flexible.scad, gregs-wade-filament-175_Flexible.stl, nozzle_mount.scad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]
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2016-03-21 Uprava parametru
    Velikost otvoru pro M6 srouby je mozne upravit pres parametr "M6_dia" v
    configuration.scad
    [corner-coupler-bottom.scad, corner-coupler.scad]
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2016-05-08 Uprava dilu pro profilove matky
    V "configuration.scad" pribyl novy parametr "profile_nut_width" (sirka
    profilove matky), ktery upravy dily pro pouziti profilovych matek.
    [RAMPS_holder.scad, configuration.scad, corner-coupler-bottom.scad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]
2016-05-08 Uprava pro dual extruder
    Vice prichytu pro zip pasky a drzak dual extruderu
    [x-carriage.scad]
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2016-05-08 Revert "Uprava pro dual extruder"
    This reverts commit cd36662e91731a72b423553a78adf4258d9adfab.
    [x-carriage_GT2.stl]
2016-05-08 Experimentalni dual extruder
    Dual extruder pro HotEnd RebelMOD v3.0
    [Dual_extruder.scad, Dual_extruder_left.stl, Dual_extruder_right.stl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]
2016-05-09 Nastavena teflonova trubicka s d=4mm
    V "settings.scad" parametr "teflon_tube_diameter = 4".
    [Dual_extruder_left.stl, Dual_extruder_right.stl, settings.scad]
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2016-08-14 Drzak pro koncove spinace X a Y
    K pridelani na 8mm tyc: M3 x 16 + maticka a podlozka.
    Pridelani endstopu: Samorezny sroubek 2,5 x 12 mm
    [endstop_X_Y-holder.scad, endstop_X_Y-holder.stl]
2016-08-14 Uprava konfigurace pro jiny pocet zeber chladice HE
    [Nozzles_30mm_fan_holder.scad, settings.scad]
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2016-10-16 Oprava kolize pro single extruder
    Oprava kolize stredoveho sloupku x-carriage s hnacim sroubem extruderu
    (pri pouziti single extruderu).
    [x-carriage.scad, x-carriage_GT2.stl]
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2017-04-03 Pridan parametr pro Z probe
    Pridana moznost vygenerovat drzak HE s otvorem pro kapacitni / indukcni
    sondu.
    [nozzle_mount.scad]
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2017-04-03 Uprava stredu velkeho kola
    Zvetseny stredovy sloupek u velkeho kola.
    [wade-gears.scad]
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2017-04-03 Pridany nove funkce
    rounded_box() - zaoblene rohy,
    zip_paska() - otvor pro stahovaci pasku,
    drazka() - drazka do hlinikoveho profilu.
    [functions.scad]
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2017-04-03 Uprava drzaku hlazene tyce
    Prodlouzen drzak hlazene tyce + ochrana M5 tyce.
    [z-top.scad, z-top.stl]
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
